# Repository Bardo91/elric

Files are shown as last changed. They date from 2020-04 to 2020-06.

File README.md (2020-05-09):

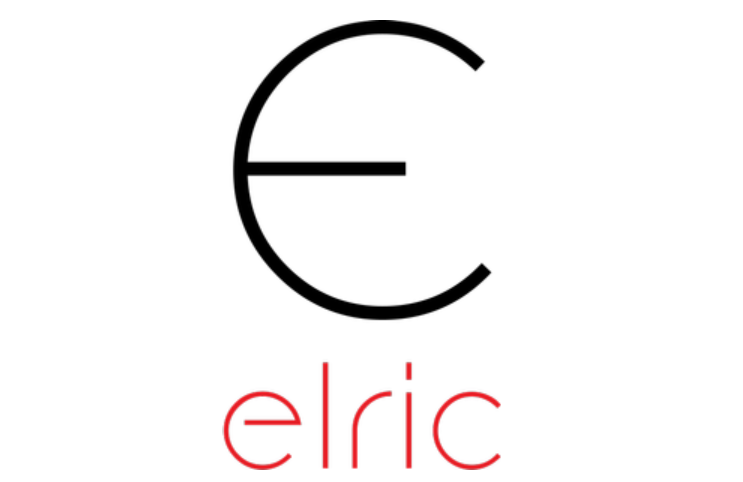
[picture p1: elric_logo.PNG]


OpenSource Robotic arm - making a dream become true

# CAD Design
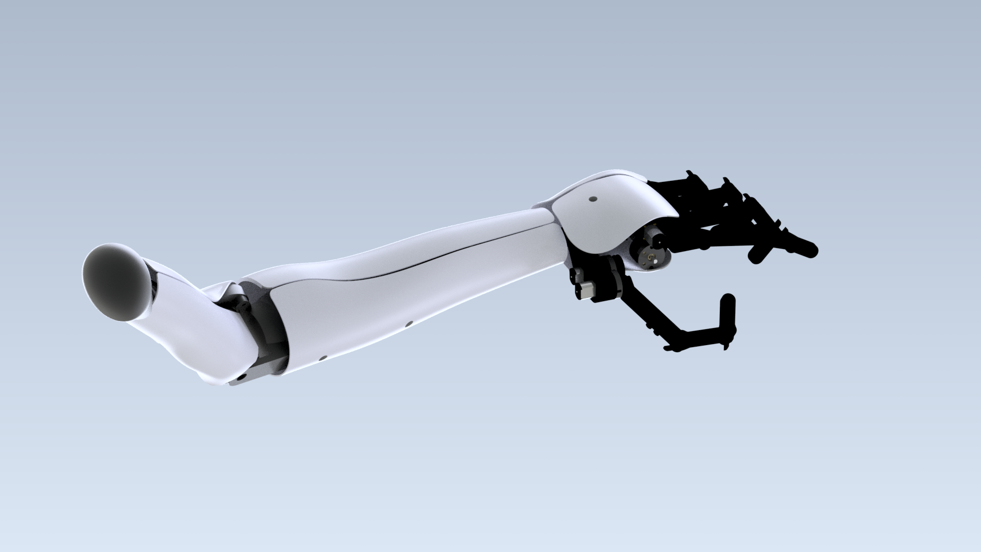
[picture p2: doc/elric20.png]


# Prototype
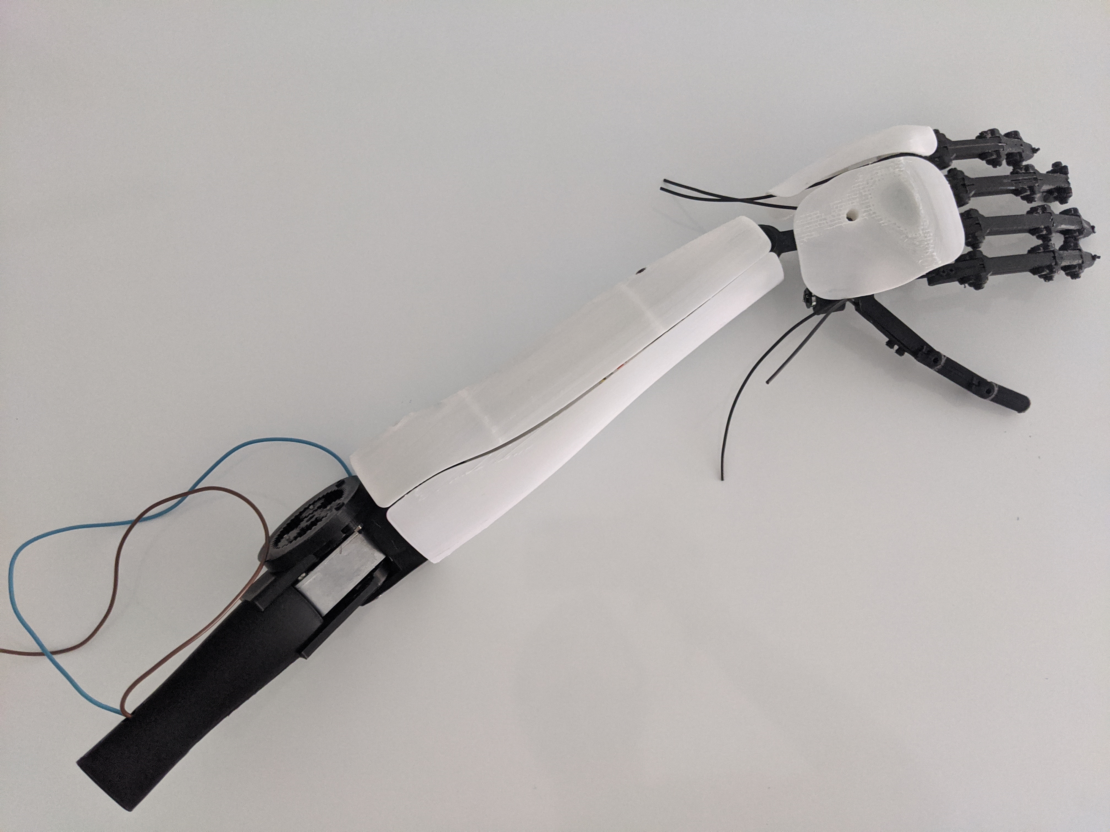
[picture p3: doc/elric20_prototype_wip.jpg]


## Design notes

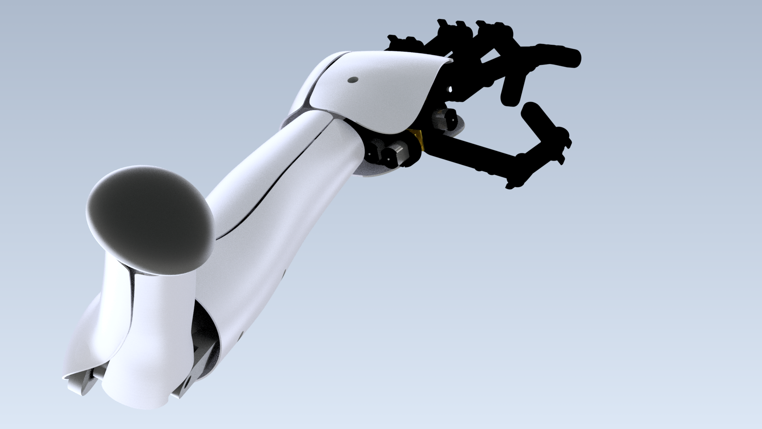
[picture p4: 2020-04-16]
elric20.png

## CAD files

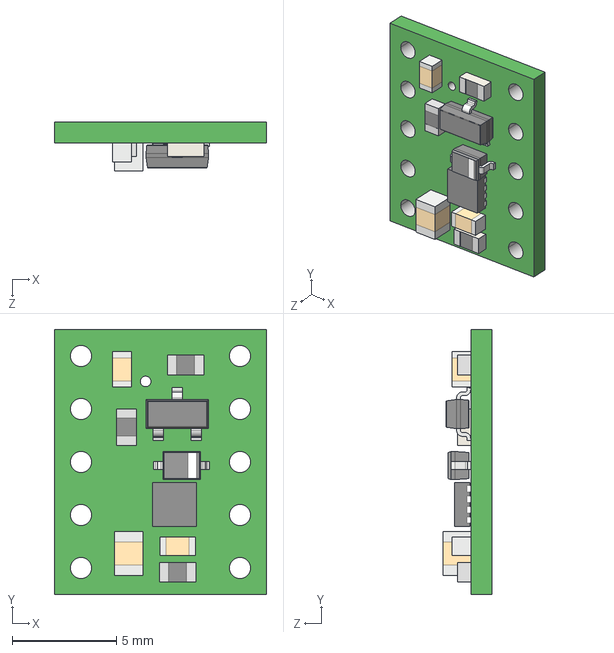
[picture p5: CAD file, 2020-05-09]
electronics/0.shared/models/drv8838-motor-driver-carrier.step
10.2 x 12.7 x 2.37 mm

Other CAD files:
hardware/0.development/pid_test_structure.ipt
hardware/0.development/test_development_pid.iam
hardware/1. hand/base_hand.ipt
hardware/1. hand/cases/hand_case_3.ipt
hardware/1. hand/elric20-01A/base_hand.ipt
hardware/1. hand/elric20-01A/cases/hand_case_1.ipt
hardware/1. hand/elric20-01A/cases/hand_case_2.ipt
hardware/1. hand/elric20-01A/cases/hand_case_3.ipt
hardware/1. hand/elric20-01A/elric20-01A.iam
hardware/1. hand/elric20-01A/finger_pulley.ipt
hardware/1. hand/elric20-01A/finger_thread_lock.ipt
hardware/1. hand/elric20-01A/index_f1.ipt
hardware/1. hand/elric20-01A/index_f2.ipt
hardware/1. hand/elric20-01A/index_f3.ipt
hardware/1. hand/elric20-01A/middle_f1.ipt
hardware/1. hand/elric20-01A/middle_f2.ipt
hardware/1. hand/elric20-01A/middle_f3.ipt
hardware/1. hand/elric20-01A/motor_dc_6v_30rpm.ipt
hardware/1. hand/elric20-01A/pinky_f1.ipt
hardware/1. hand/elric20-01A/pinky_f2.ipt
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

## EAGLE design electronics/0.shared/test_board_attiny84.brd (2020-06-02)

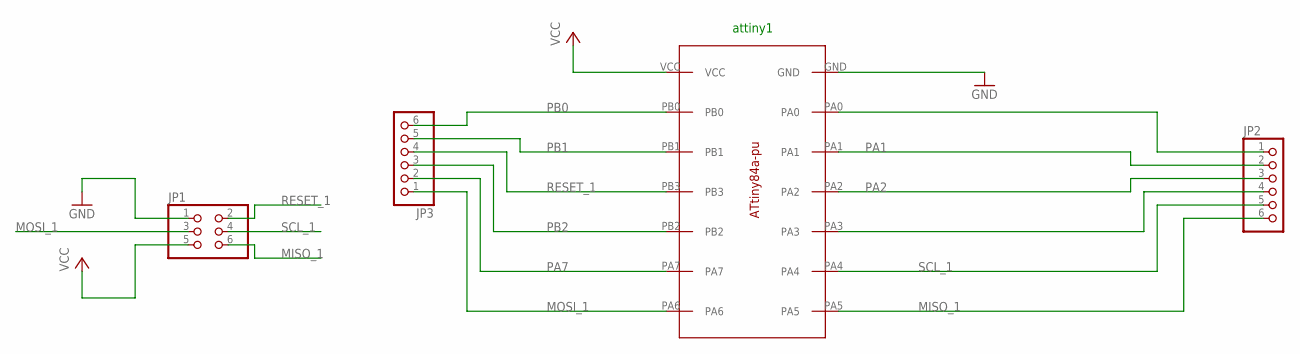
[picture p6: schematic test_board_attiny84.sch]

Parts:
JP1: PINHD-2X3; 2X03
JP2, JP3: PINHD-1X6; 1X06
U$8: ATTINY84A-PU

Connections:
GND: JP1.1, U$8.GND
MISO_1: JP1.6, JP2.6, U$8.PA5
MOSI_1: JP1.3, JP3.1, U$8.PA6
unnamed: JP2.1, U$8.PA0
PA1: JP2.2, U$8.PA1
PA2: JP2.3, U$8.PA2
PA3: JP2.4, U$8.PA3
PA7: JP3.2, U$8.PA7
PB0: JP3.6, U$8.PB0
PB1: JP3.5, U$8.PB1
PB2: JP3.3, U$8.PB2
RESET_1: JP1.2, JP3.4, U$8.PB3
SCL_1: JP1.4, JP2.5, U$8.PA4
VCC: JP1.5, U$8.VCC

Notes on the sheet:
attiny1

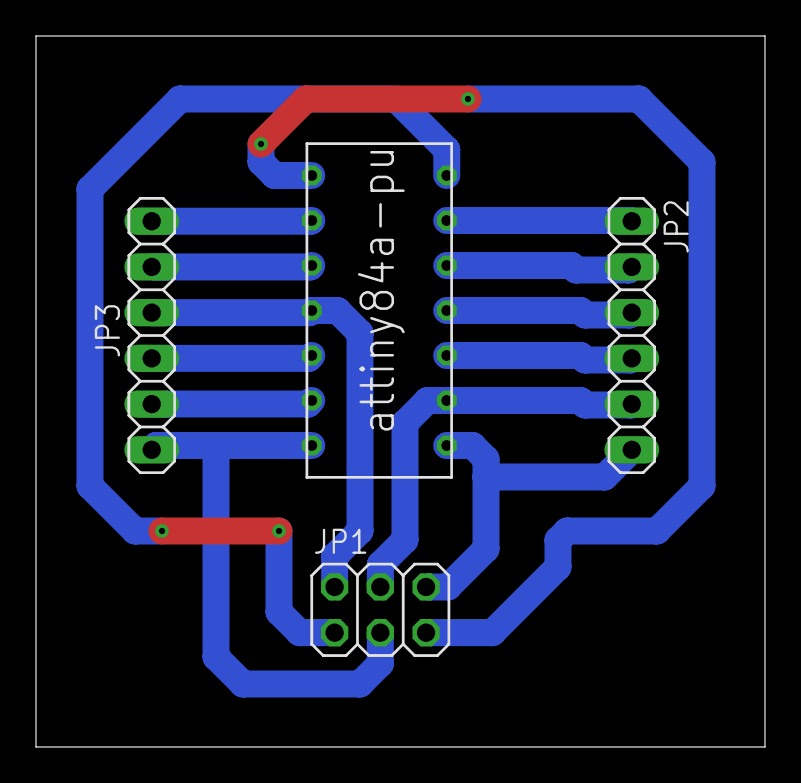
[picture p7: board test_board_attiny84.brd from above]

Board: 2 copper layers, 40.5 x 39.5 mm, 4 parts (0 on the bottom side), 14 nets.

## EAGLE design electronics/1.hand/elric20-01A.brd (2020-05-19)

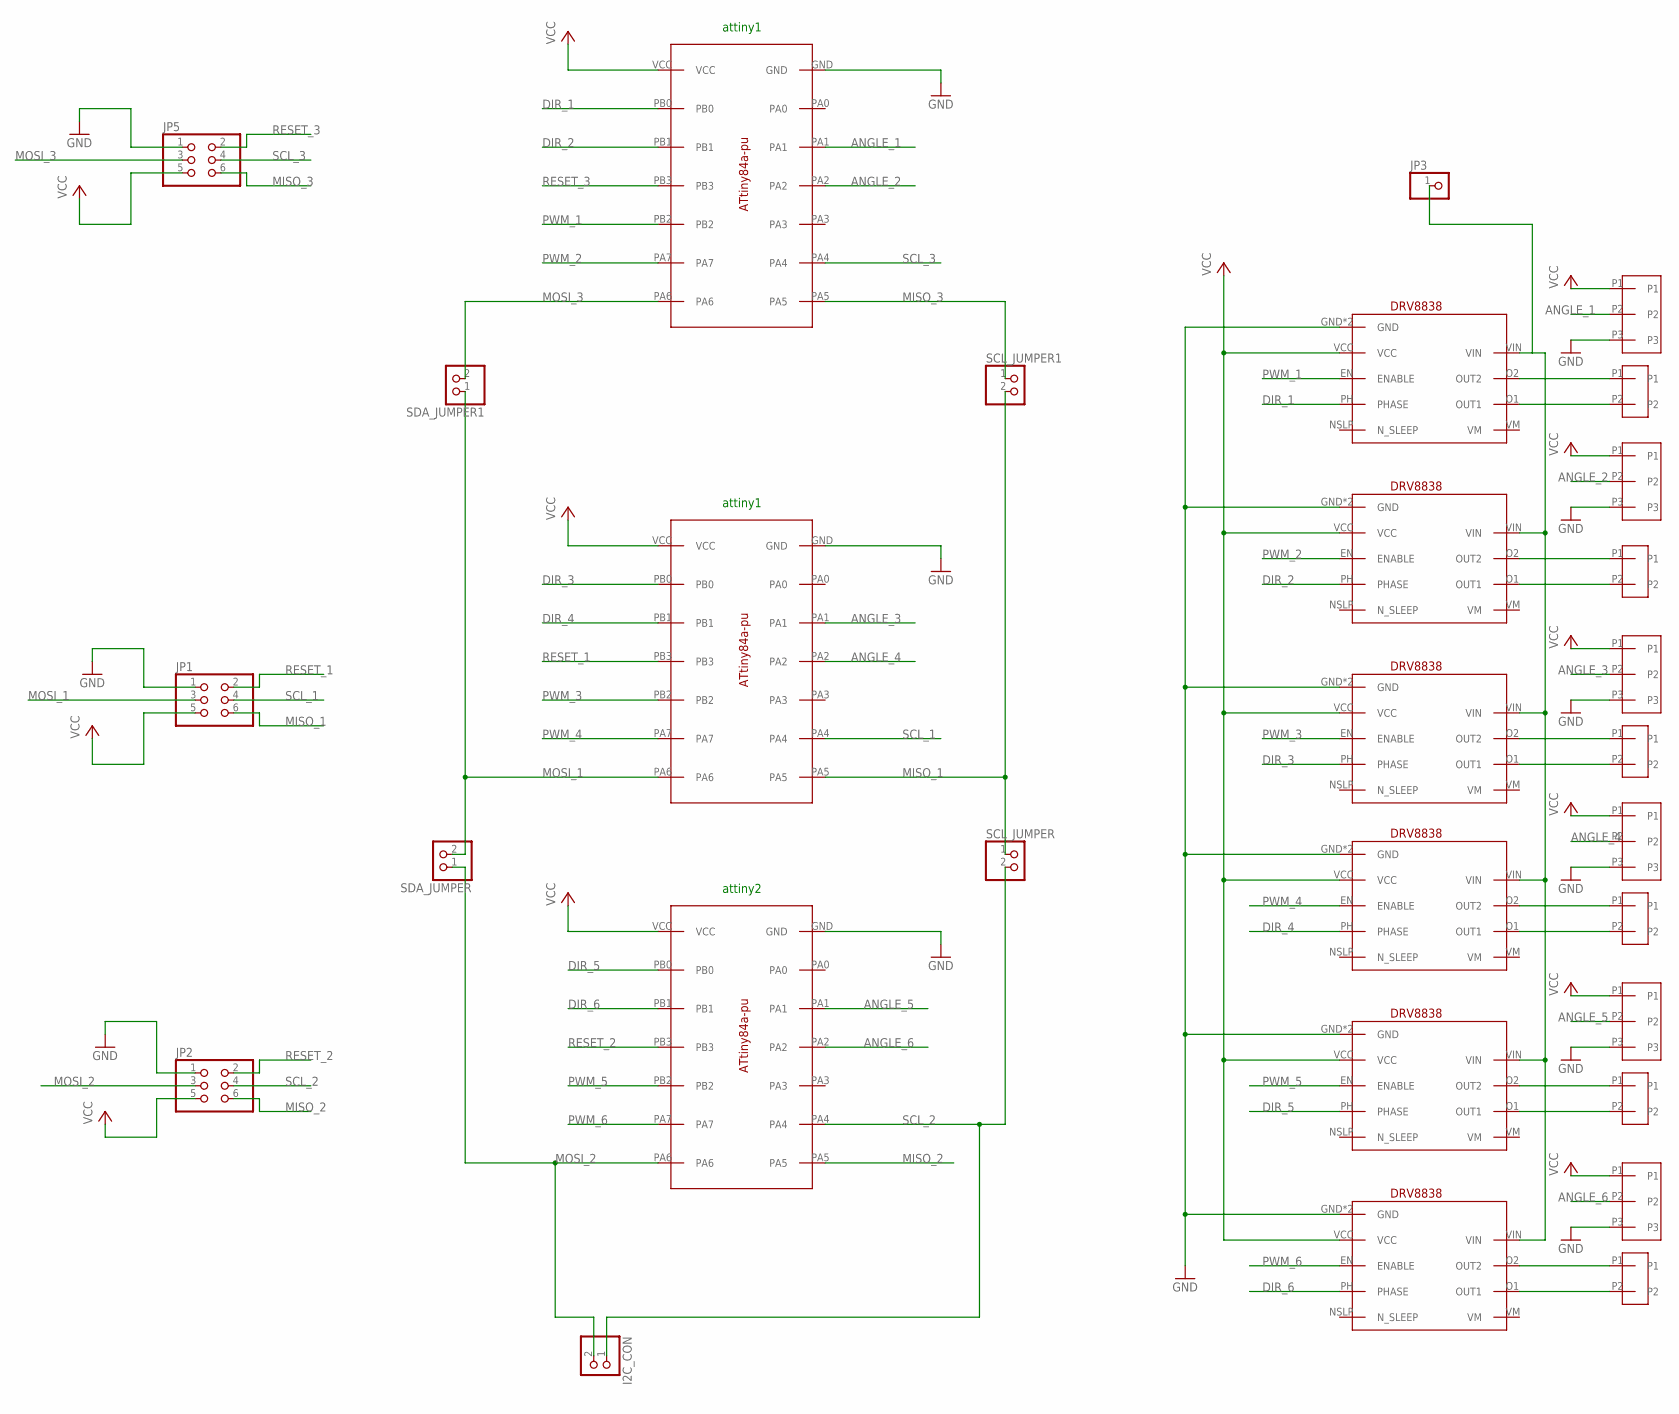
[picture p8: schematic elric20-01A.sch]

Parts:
I2C_CON: PINHD-1X2; 1X02
JP1, JP2, JP5: PINHD-2X3; 2X03
JP3: PINHD-1X1; 1X01
SCL_JUMPER, SCL_JUMPER1: PINHD-1X2; 1X02
SDA_JUMPER, SDA_JUMPER1: PINHD-1X2; 1X02
U$1, U$8, U$21: ATTINY84A-PU
U$2, U$3, U$4, U$5, U$6, U$7: DRV8838
U$9, U$10, U$11, U$12, U$13, U$14: PAD_SMD_X2_BIG
U$15, U$16, U$17, U$18, U$19, U$20: PAD_SMD_X3

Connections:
ANGLE_1: U$20.P2, U$21.PA1
ANGLE_2: U$19.P2, U$21.PA2
ANGLE_3: U$8.PA1, U$18.P2
ANGLE_4: U$8.PA2, U$17.P2
ANGLE_5: U$1.PA1, U$16.P2
ANGLE_6: U$1.PA2, U$15.P2
DIR_1: U$2.PH (PHASE), U$21.PB0
DIR_2: U$3.PH (PHASE), U$21.PB1
DIR_3: U$4.PH (PHASE), U$8.PB0
DIR_4: U$5.PH (PHASE), U$8.PB1
DIR_5: U$1.PB0, U$6.PH (PHASE)
DIR_6: U$1.PB1, U$7.PH (PHASE)
GND: JP1.1, JP2.1, JP5.1, U$1.GND, U$2.GND, U$2.GND2 (GND), U$3.GND, U$3.GND2 (GND), U$4.GND, U$4.GND2 (GND), U$5.GND, U$5.GND2 (GND), U$6.GND, U$6.GND2 (GND), U$7.GND, U$7.GND2 (GND), U$8.GND, U$15.P3, U$16.P3, U$17.P3, U$18.P3, U$19.P3, U$20.P3, U$21.GND
MISO_1: JP1.6, SCL_JUMPER.1, SCL_JUMPER1.2, U$8.PA5
MISO_2: JP2.6, U$1.PA5
MISO_3: JP5.6, SCL_JUMPER1.1, U$21.PA5
MOSI_1: JP1.3, SDA_JUMPER.2, SDA_JUMPER1.1, U$8.PA6
MOSI_2: I2C_CON.2, JP2.3, SDA_JUMPER.1, U$1.PA6
MOSI_3: JP5.3, SDA_JUMPER1.2, U$21.PA6
unnamed: U$2.O2 (OUT2), U$9.P1
unnamed: U$2.O1 (OUT1), U$9.P2
unnamed: U$3.O2 (OUT2), U$10.P1
unnamed: U$3.O1 (OUT1), U$10.P2
unnamed: U$4.O2 (OUT2), U$11.P1
unnamed: U$4.O1 (OUT1), U$11.P2
unnamed: U$5.O2 (OUT2), U$12.P1
unnamed: U$5.O1 (OUT1), U$12.P2
unnamed: U$6.O2 (OUT2), U$13.P1
unnamed: U$6.O1 (OUT1), U$13.P2
unnamed: U$7.O2 (OUT2), U$14.P1
unnamed: U$7.O1 (OUT1), U$14.P2
unnamed: JP3.1, U$2.VIN, U$3.VIN, U$4.VIN, U$5.VIN, U$6.VIN, U$7.VIN
PWM_1: U$2.EN (ENABLE), U$21.PB2
PWM_2: U$3.EN (ENABLE), U$21.PA7
PWM_3: U$4.EN (ENABLE), U$8.PB2
PWM_4: U$5.EN (ENABLE), U$8.PA7
PWM_5: U$1.PB2, U$6.EN (ENABLE)
PWM_6: U$1.PA7, U$7.EN (ENABLE)
RESET_1: JP1.2, U$8.PB3
RESET_2: JP2.2, U$1.PB3
RESET_3: JP5.2, U$21.PB3
SCL_1: JP1.4, U$8.PA4
SCL_2: I2C_CON.1, JP2.4, SCL_JUMPER.2, U$1.PA4
SCL_3: JP5.4, U$21.PA4
VCC: JP1.5, JP2.5, JP5.5, U$1.VCC, U$2.VCC, U$3.VCC, U$4.VCC, U$5.VCC, U$6.VCC, U$7.VCC, U$8.VCC, U$15.P1, U$16.P1, U$17.P1, U$18.P1, U$19.P1, U$20.P1, U$21.VCC

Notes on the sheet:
attiny1
attiny2

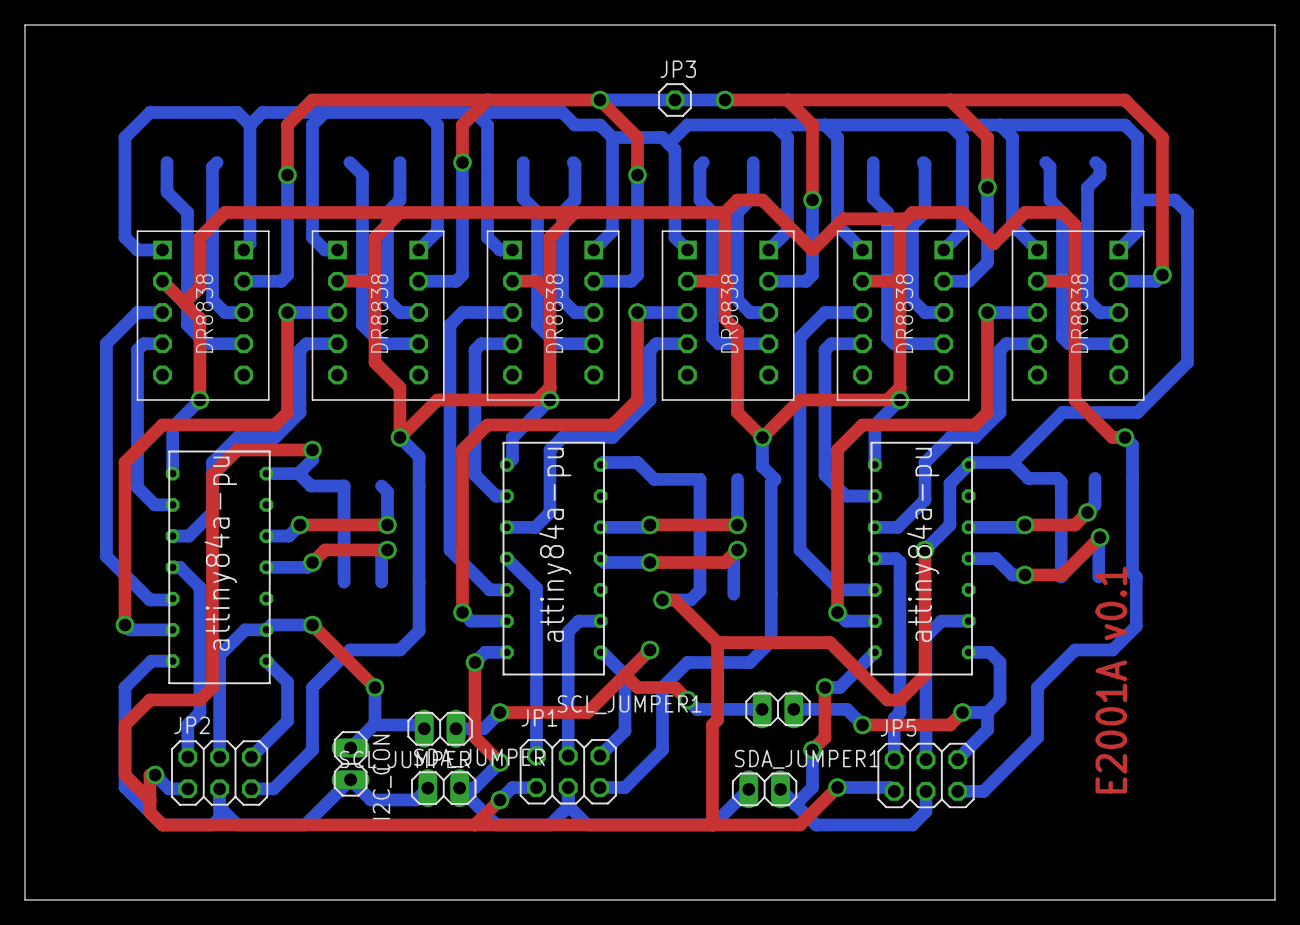
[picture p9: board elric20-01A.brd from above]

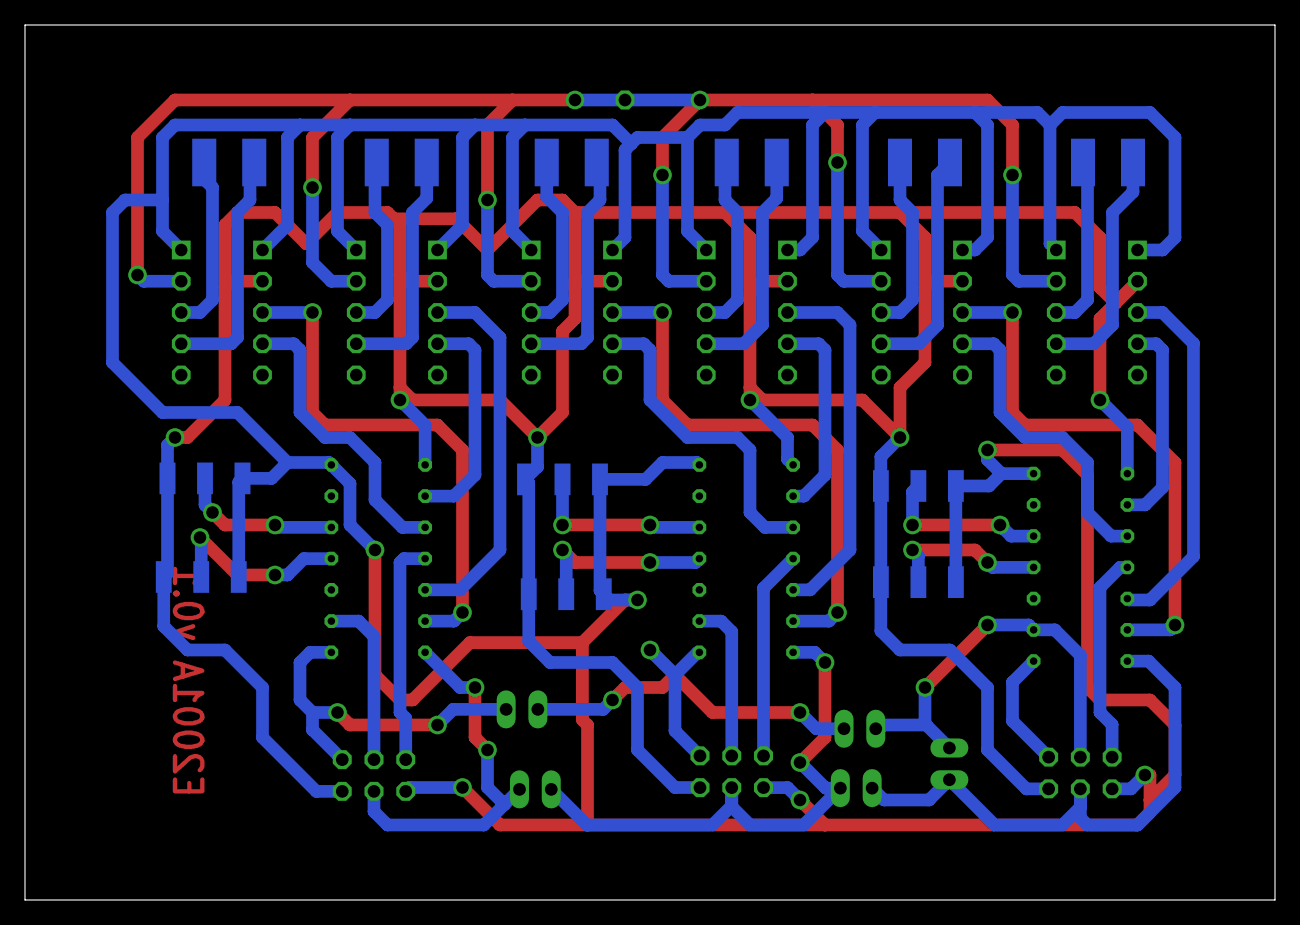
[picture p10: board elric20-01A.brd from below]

Board: 2 copper layers, 100.0 x 70.0 mm, 30 parts (12 on the bottom side), 45 nets.

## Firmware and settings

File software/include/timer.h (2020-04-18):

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
//  Maintainer: pabramsor@gmail.com
//
//---------------------------------------------------------------------------------------------------------------------

#ifndef ELRIC_HAL_TIMER_H_
#define ELRIC_HAL_TIMER_H_

#include <register.h>

namespace elric{

    enum TimerModes {
        normal = 0,
        PWM_phase_correct_MAX,
        CTC,
        fast_PWM_MAX,
        /* 4 Reserved */
        PWM_phase_correct_TOP = 5,
        /* 6 Reserved */
        fast_PWM_TOP = 7
    };

    enum PrescalerModes {
        no_clock = 0,
        no_prescaler,
        prescaler_8,
        prescaler_64,
        prescaler_256,
        prescaler_1024,
        external_clock_falling,
        external_clock_rising,
    };

    enum CompareModeNormal{
        cmn_disconected = 0,
        cmn_toggle,
        cmn_clear,
        cmn_set
    };

    enum CompareModeFastPWM{
        fpwm_disconnected = 0,
        fpwm_reserved,
        fpwm_non_inverting,
        fpwm_inverting
    };

    enum CompareModePhaseCorrectPWM{
        pcpwm_disconnected = 0,
        pcpwm_reserved,
        pcpwm_setRegisterOnMatch,
        pcpwm_clearRegisterOnMatch
    };
    

    template<typename RegisterTraits_>
    class Timer{
    public:
        void setMode(TimerModes _mode);
        
        void setCompareModeA(uint8_t _mode);
        void setCompareA(uint8_t _mode);

        void setCompareModeB(uint8_t _mode);
        void setCompareB(uint8_t _mode);
        
        void setPrescaler(uint8_t _prescaler);

    private:
        // Registers
        Register<uint8_t, RegisterTraits_::tccr0A>   controlRegisterA_;
        Register<uint8_t, RegisterTraits_::tccr0B>   controlRegisterB_;
        Register<uint8_t, RegisterTraits_::tcnt0>    counterRegister_;
        Register<uint8_t, RegisterTraits_::ocr0A>    outputCompareRegisterA_;
        Register<uint8_t, RegisterTraits_::ocr0B>    outputCompareRegisterB_;
        Register<uint8_t, RegisterTraits_::timsk>    interruptMaskRegister_;
        Register<uint8_t, RegisterTraits_::tifr>     interruptFlagRegister_;

    };

}

#include <timer.inl>

#endif

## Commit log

2020-04-09 Init files
    [base_hand.ipt, hand.iam, index_f1.ipt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]
2020-04-09 pinky v2.0 working mechanism.
    [base_hand.ipt, finger_pulley.ipt, finger_thread_lock.ipt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]
2020-04-10 Four fingers v2.0
    [base_hand.ipt, hand.iam, index_f1.ipt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]
2020-04-10 thumb and partial case
    [base_hand.ipt, hand.iam, hand_case_1.ipt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]
2020-04-11 Added 3rd case to hand and added logo
    [base_hand.ipt, hand.iam, hand_case_1.ipt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]
2020-04-11 dummy wrist joint
    [base_hand.ipt, hand.iam, hand_case_1.ipt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]
2020-04-11 minor changes in case
    [hand_case_2.ipt]
2020-04-12 Renamed folders and files according to new nomemclature
    [base_hand.ipt, elric20-1A.iam, elric20.iam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]
2020-04-12 Fixed hand motors holders. Case fixes. Added arm assembly.
    [base_hand.ipt, elric20-1A.iam, elric20-2A.iam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]
2020-04-12 Renamed assemblies. Added forearm and forearm cases
    [arm_case_1.ipt, arm_case_2.ipt, elric20-01A.iam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]
2020-04-12 Fixes in arm_case
    [arm_case_1.ipt, arm_case_2.ipt, elric20.iam]
2020-04-12 first draft forearm. WIP: arm
    [arm.ipt, elbow_1.iam, elbow_gear_ext.ipt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]
2020-04-13 Finish hand case attachment and minor fixes
    [base_hand.ipt, elric20-01A.iam, elric20-02A.iam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]
2020-04-13 WIP: elbow engine
    [Spur Gears3.iam, arm.ipt, elbow_1.iam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]
2020-04-13 First version elbow
    [arm.ipt, elbow_gear_int_2.ipt, elric20-01A.iam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]
2020-04-15 Arm finished with case and attachments
    [arm_case_1.ipt, arm_case_2.ipt, elric20-01A.iam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]
2020-04-16 case arm and forearm
    [arm_case_1.ipt, arm_case_2.ipt, elric20-01A.iam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]
2020-04-17 ribbed case foream 2
    [elric20-02A.iam, elric20.iam, forearm_case_2.ipt]
2020-04-18 Fixed register address, working library for gpio. next pwm!
2020-04-18 working raw pwm test
2020-04-18 coded 8 bit timer
2020-04-18 renamed examples, added timer to attiny84, generalized examples.
2020-04-25 Printing new version of elbow to test joint.
    [arm.ipt, elbow_gear_int_1.ipt, elric20-02A.iam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]
2020-04-25 WIP: ADC
2020-04-25 WIP: debugging ADC
2020-04-25 working ADC
2020-04-25 working adc and pwm but OCR0A set value
2020-04-25 Fixed register set value. Working ADC and PWM
    [attiny_pwm.cpp]
2020-04-26 Fixes in elbow related with dimensions of servo. Rework of motor_dc_6v_30rpm.ipt. Created test structure for PID software
    [arm.ipt, elbow_gear_int_2.ipt, elric20-01A.iam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]
2020-04-28 many things... I do not remember XD sorry
    [arm.ipt, arm_case_2.ipt, elric20-02A.iam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]
2020-05-09 Fixes in hand joint engines
    [base_hand.ipt, elric20-01A.iam, elric20.iam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]
2020-05-09 WIP elric20-01A electronics
    [drv8838-motor-driver-carrier.step, elric20-01A.sch, potentiometer_holder.ipt]
2020-05-09 Updated potentiometer_holder.ipt so it can be flipped
    [elric20-01A.iam, elric20.iam, potentiometer_holder.ipt]
2020-05-09 Elric20 images
    [base_hand.ipt, elric20-01A.iam, elric20.iam]
2020-05-10 First version hand electronics
    [elbow_gear_int_2.ipt, elric20-01A.brd, elric20-01A.sch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]
2020-05-10 Added board name and version
    [elric20-01A.brd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]
2020-05-19 New version of hand electronics. Packed in servos 2 by 2
    [elric20-01A.brd, elric20-01B.brd, elric20-01B.sch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]
2020-05-31 Moved elric20-01A files to an old folder. Created elric20-01B. New finger design, but thumb.
    [base_hand.ipt, elric20-01A.iam, elric20-01B.iam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]
2020-06-02 Fixes in base hand
    [base_hand.ipt, elric20-01B.iam]
2020-06-02 Added developer board for ATtiny84
    [test_board_attiny84.brd, test_board_attiny84.sch]

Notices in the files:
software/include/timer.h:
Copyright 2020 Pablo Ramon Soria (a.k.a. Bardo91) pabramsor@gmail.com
